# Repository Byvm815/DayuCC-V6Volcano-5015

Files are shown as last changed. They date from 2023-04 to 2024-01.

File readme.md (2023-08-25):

# 项目说明
## 托管
本项目使用Git做数据管理，托管在[Github](https://github.com/Byvm815/DayuCC-V6Volcano-5015)

如果你是在大鱼QQ群里下载的，建议你在下载后拉取更新

## 推荐的方案
我推荐你使用最新的V6方案B，也是我比较满意的方案。

需要说明的是，方案B的设计在大鱼TT公布前就已经想好了，没有抄袭TT的风道。

# 技术路线（摘抄自本人笔记）
## CR10路线
### 原版散热器，v6火山
优点：便宜、cc原版散热器，适配性最好、火山加热块可直接使用

缺点：喉管只有一个顶丝固定点，长时间的稳定性差、喉管接触方式导致接触面积小，喉管导热不佳（可通过硅脂解决）。稳定性差点，价格最便宜。

### 原版散热器，适配版火山加热块
优点：CC的理想热端、原版的双螺丝稳定、火山长度加热区

缺点：目前而言，没有硅胶套（但是我问客服，有非量产版的）、喉管的接触方式导致接触面积小，喉管导热不佳（可通过硅脂解决）。价格太贵，加上买喉管的钱，都够买cr10s（方块状）一套了。

### cr10（v6螺纹）散热器，v6火山加热块
优点：配件总价格最便宜、我想要的cr10散热器外形配v6喉管

缺点：散热片太少（暂时不确定是否有影响，因为螺纹有效地增大了喉管与散热器的接触面积）。就算散热够用，性价比也没有cr10s pro打印一个增高垫的方案高。

### cr10s散热器（方块状），v6火山
优点：直接使用m7的双金属喉管，CR10路线性价比最高的方案，到手可用。风道使用原版加长即可。

缺点：喉管中下段往上，喉管裸露，散热面积较小

### cr10s pro散热器，v6火山
优点：皆据上述的散热器优点：v6螺纹、多散热片、直接使用v6加热块、独有的双顶丝固定。

缺点：气动接头的位置过于靠上，在不安装气动接头的情况下，位置刚刚够用，无法直接安装气动接头（主要是空间大，挤出的耗材容易折弯）（我已经想到解决办法了。一，给电机底座加个垫片，再使用隐藏式的气动接头，通入特氟龙管。二，直接限制内部空间，具体设计有难度）（通过淘宝的散热器类型可知，这个就是参考cr6的散热器上端设计的，原版的cr6和cr10一样，气动接头安装的地方是平的，只是cr6要使用一个额外的延长座，结果cr10s pro直接把延长座和散热器合体了）

### cr10散热器外观的拓竹热端
优点：CC的理想热端

缺点：和cr10一样喉管导热差、很贵

## v6路线
之前一直想找螺纹长的铜柱，没有理想的。今天走狗屎运碰到了，m3*30+10，虽然螺纹长度差了一点，但拧入距离也有6mm了，完全够用。（其实可以通过两个铜柱连接的方式取代这个理想铜柱，我是傻瓜）

可以将固定''热端安装板''的螺丝替换成铜柱，就能在固定的同时，提供风扇固定孔了。这样，就可以使用cnc的金属v6固定座。风扇通过螺丝加紧固定，也比打印的孔位牢靠。

## 总结
CR10路线的散热器，便宜的没有一个是设计优秀的，设计优秀的又贵得要死（主要还是散热器无法单独购买）。

所以还得是V6，用网上的热门话语来说就是：V6 永远的神！

目前还没有理想的自动调平的方案（大鱼做的时候没考虑，硬件缺陷），代思路明确再设计验证。

# 开源许可证
本项目以AGPL协议开源。禁止商用，禁止售卖资料！

一切违背开源协议、侵犯原作者著作权、占有他人劳动成果用于盈利的行为，需自行承担法律风险！

# 捐赠
设计、测试、整理不易，可以捐赠1、2块。就当是研发费了。

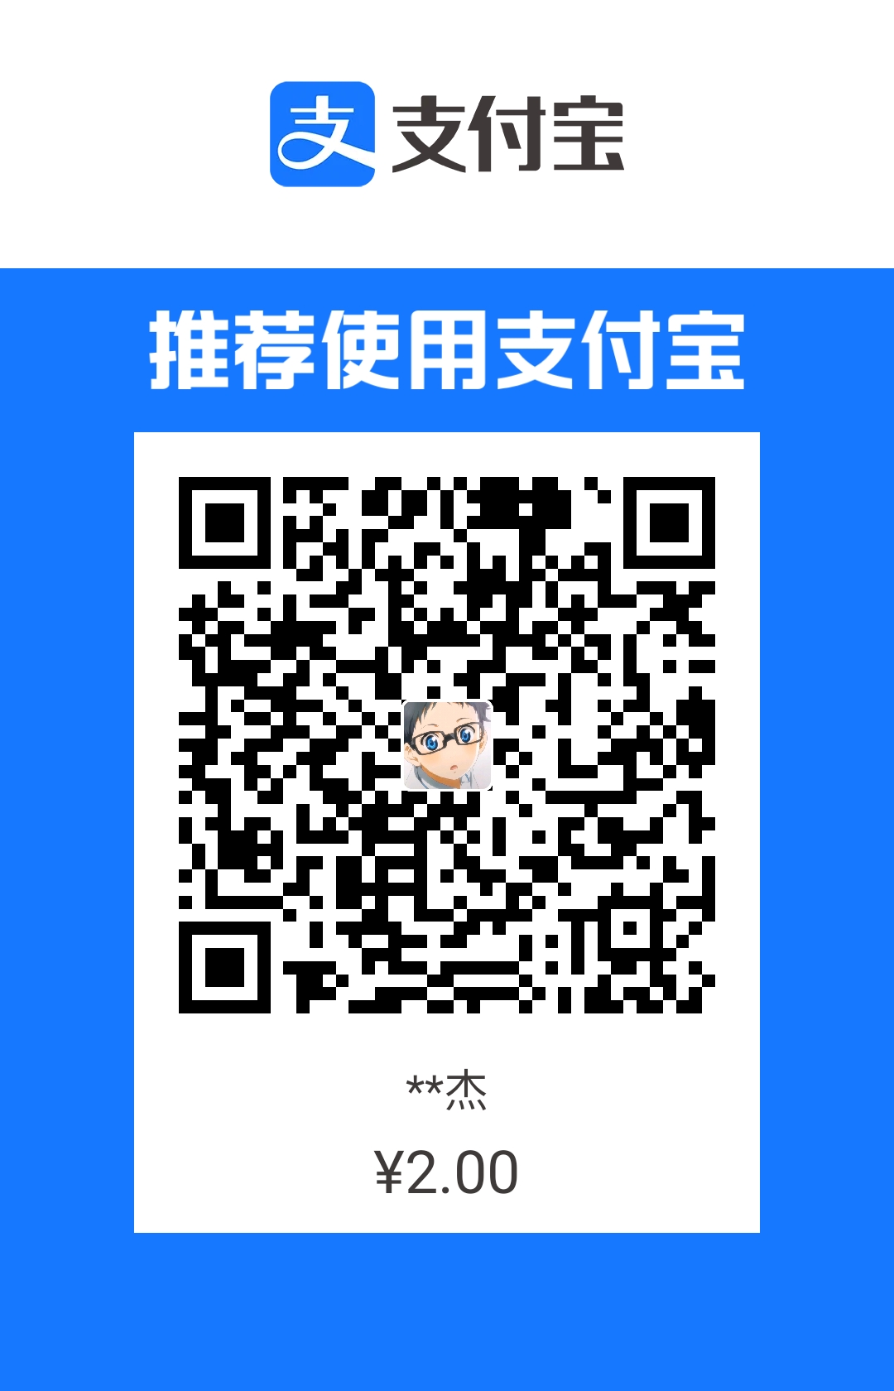
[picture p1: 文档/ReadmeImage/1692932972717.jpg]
收款码


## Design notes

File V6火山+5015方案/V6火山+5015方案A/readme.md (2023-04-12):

# 白雨木的说明

## 效果图（图片仅供参考）
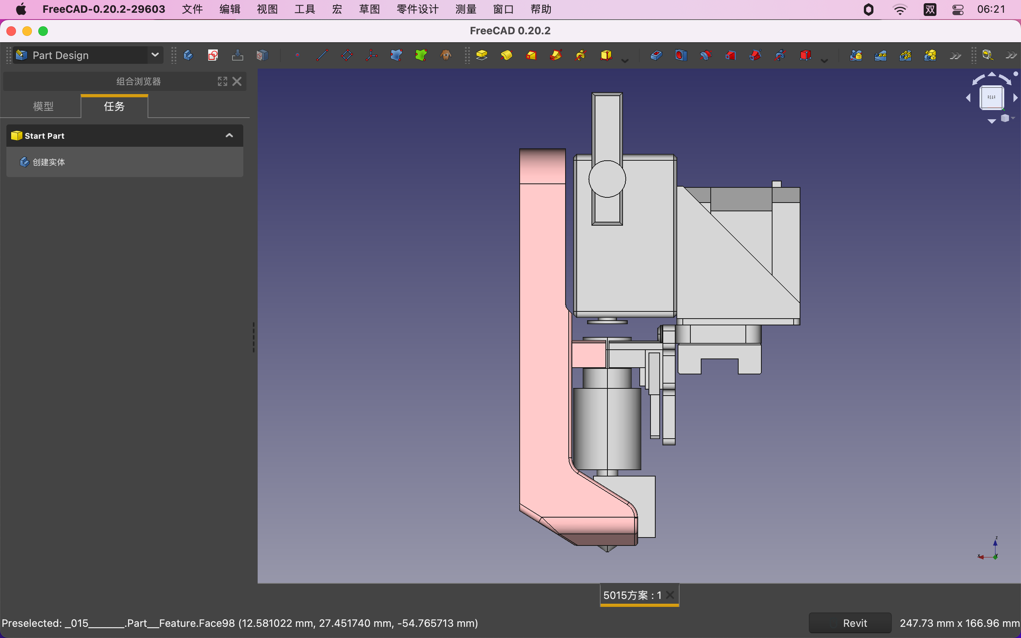
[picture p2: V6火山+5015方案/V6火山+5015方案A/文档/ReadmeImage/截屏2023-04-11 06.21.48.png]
截屏


## 物料清单：
1. [5015液压风扇](https://item.taobao.com/item.htm?spm=a1z09.2.0.0.4e562e8dwG9V3d&id=654878833029&_u=b3u8db4m4d76)
2. [M3*50螺丝](https://detail.tmall.com/item.htm?_u=b3u8db4mfd2b&id=636577427255&spm=a1z09.2.0.0.4e562e8dwG9V3d)
3. [M4*15对锁螺丝](https://detail.tmall.com/item.htm?id=542579355142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)
4. [E3DV6近程散热器](https://item.taobao.com/item.htm?spm=a1z10.3-c-s.w4002-17331600343.22.254e3e69IKgMQ4&id=559984859809)
5. [不锈钢喉管（不带铁氟龙）](https://item.taobao.com/item.htm?id=559690409325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)（双金属带外六角的喉管，比常规喉管长，我现在没有实物，故模型暂未适配）
6. [V6火山PT100铝加热块](https://item.taobao.com/item.htm?spm=a1z10.3-c-s.w4002-17331600343.29.c8e43e69NdG7as&id=680651648360)（推荐购买此加热块）
7. [热敏电阻](https://item.taobao.com/item.htm?spm=a1z10.3-c-s.w4002-17331600343.50.40003e6958S0JV&id=575202356478)（按加热块型号购买）
8. [硅胶套](https://item.taobao.com/item.htm?spm=a1z10.3-c-s.w4002-17331600343.19.c8e43e69uqzWFz&id=633630275262)（按加热块型号购买）
9. [火山喷嘴](https://item.taobao.com/item.htm?spm=a1z10.3-c-s.w4002-17331600343.38.436d3e69l3Q1HW&id=691269644652)

10. 3010风扇（CC清单已购）
11. M3*14螺丝（CC清单已购）
12. 加热棒（CC清单已购）
13. M3*10螺丝（CC清单已购）

不含已购物料和运费，共计38.91元。含运费，共计43.91元。

## 切片说明（以PrusaSlicer为例）
导风口需按以下条件进行特殊设置：
1. 0.4打印喷嘴，需要将“最小轮廓数”改为2，以便搭桥起点下方不悬空
2. （填充图案为星型时）“填充率”至少设为40%
3. 取消“自动生成支撑”，导风口可无支撑打印

贴墙端需按以下条件进行设置：
1. （填充图案为星型时）“填充率”至少设为40%

切片摆放方向：螺丝孔洞与Z轴平行。

## 改进空间
1. 取消3010风扇安装座，直接在开口平面上安装3015风扇，理论上与散热器之间有0.4mm距离
2. 贴墙端固定件可使用热熔滚花螺母

## Github
[项目地址](https://github.com/Byvm815/DayuCC-V6Volcano-5015)

## 开源许可证
本项目的导风口作者为【大鱼DIY】（以下简称“原作者”），原作者授权给白雨木进行二次更改并允许开源。原作者的开源条件是：开源后不可进行商用，故本项目以AGPL协议开源。禁止商用，禁止售卖资料！

一切违背开源协议、侵犯原作者著作权、占有他人劳动成果用于盈利的行为，需自行承担法律风险！

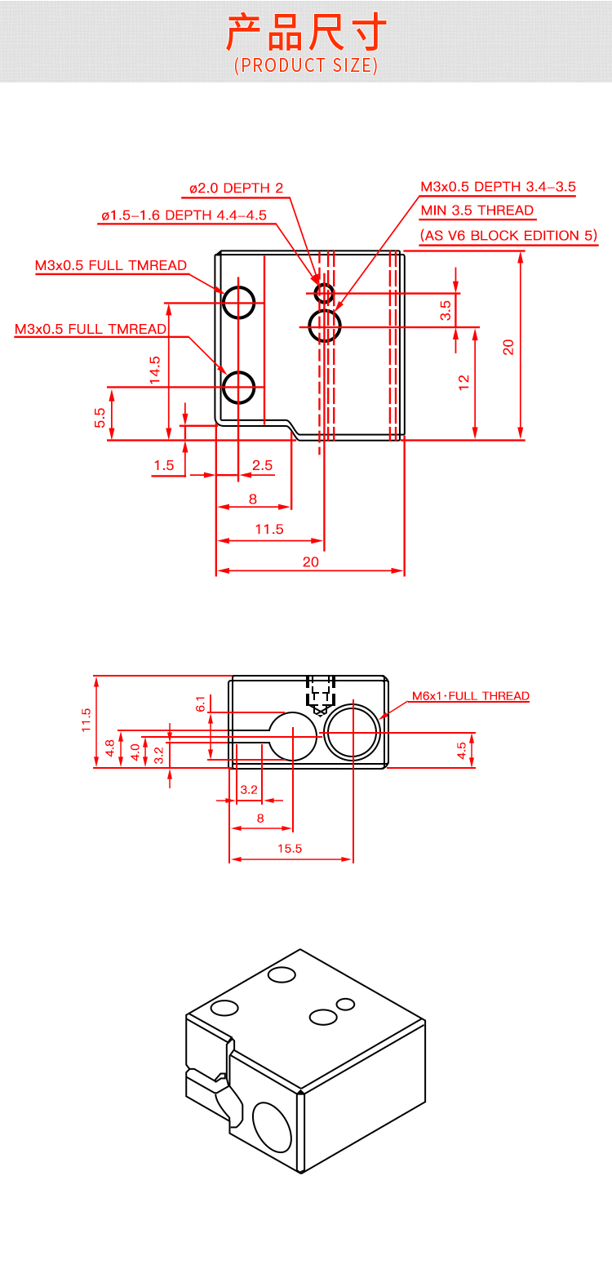
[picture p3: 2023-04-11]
V6火山+5015方案/参考资料/O1CN012gRX7m1FdcYz98SY7_!!3878490510.jpg

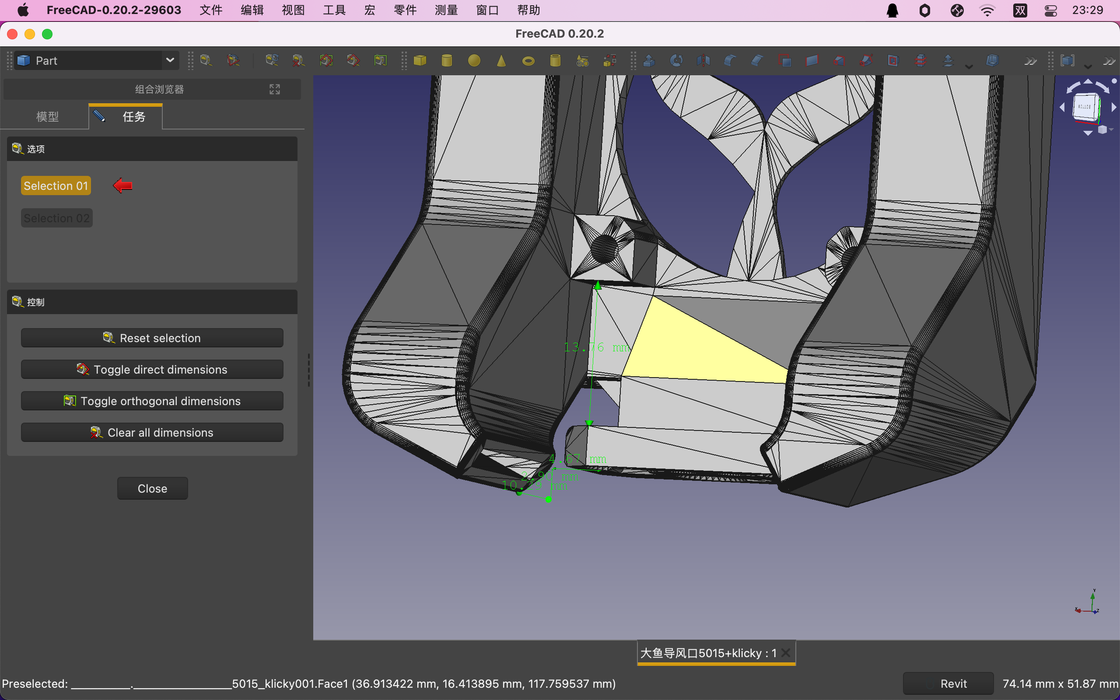
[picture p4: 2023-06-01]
V6火山+5015方案/参考资料/截屏2023-05-20 23.29.21.png

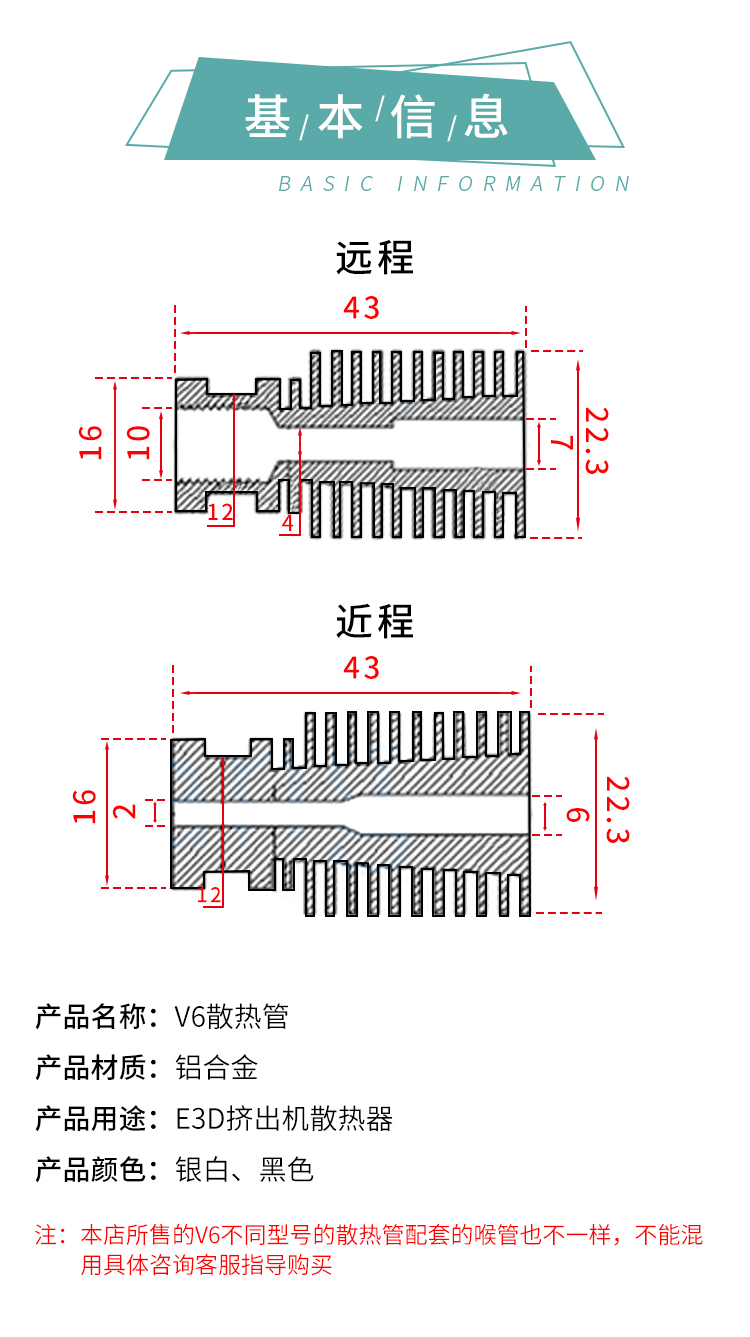
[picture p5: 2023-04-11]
V6火山+5015方案/参考资料/O1CN01hj3WWK1FdcZCZzyd2_!!3878490510.jpg

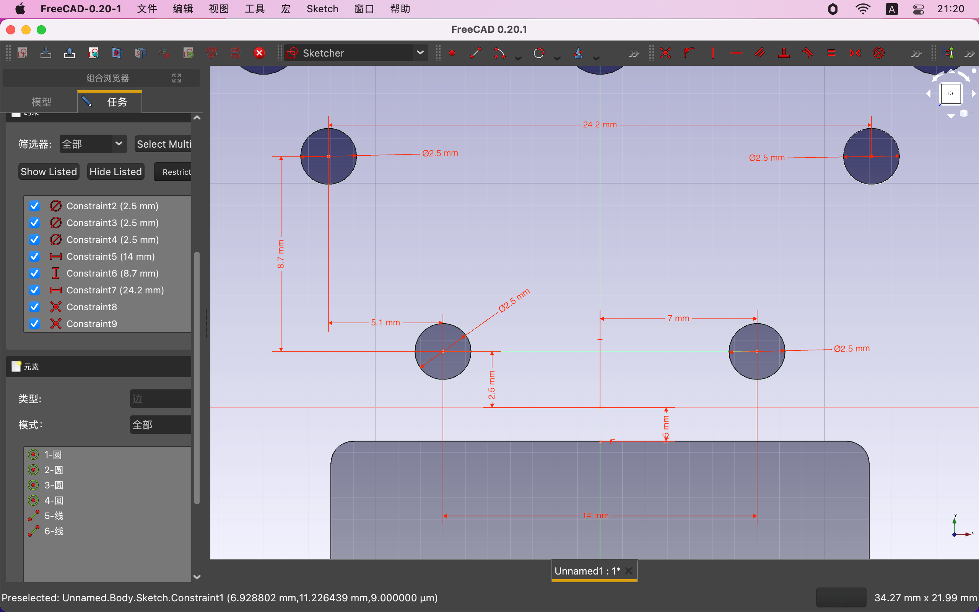
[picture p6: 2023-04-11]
V6火山+5015方案/参考资料/截屏2023-01-09 21.20.55.png

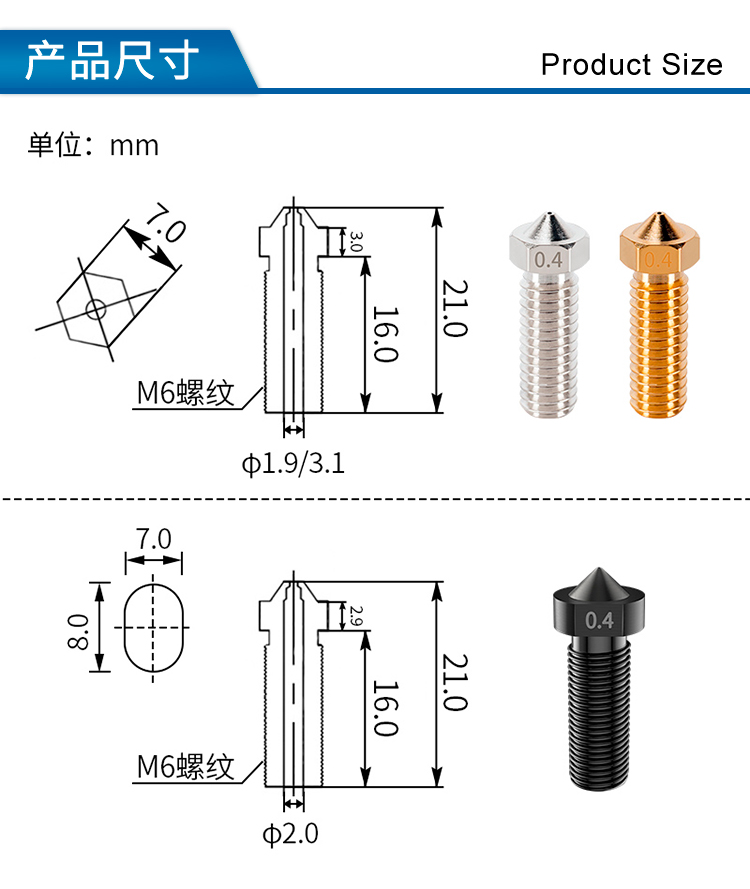
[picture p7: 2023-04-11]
V6火山+5015方案/参考资料/O1CN01lO3DwQ2JRxHx6H1lr_!!3319579419.jpg

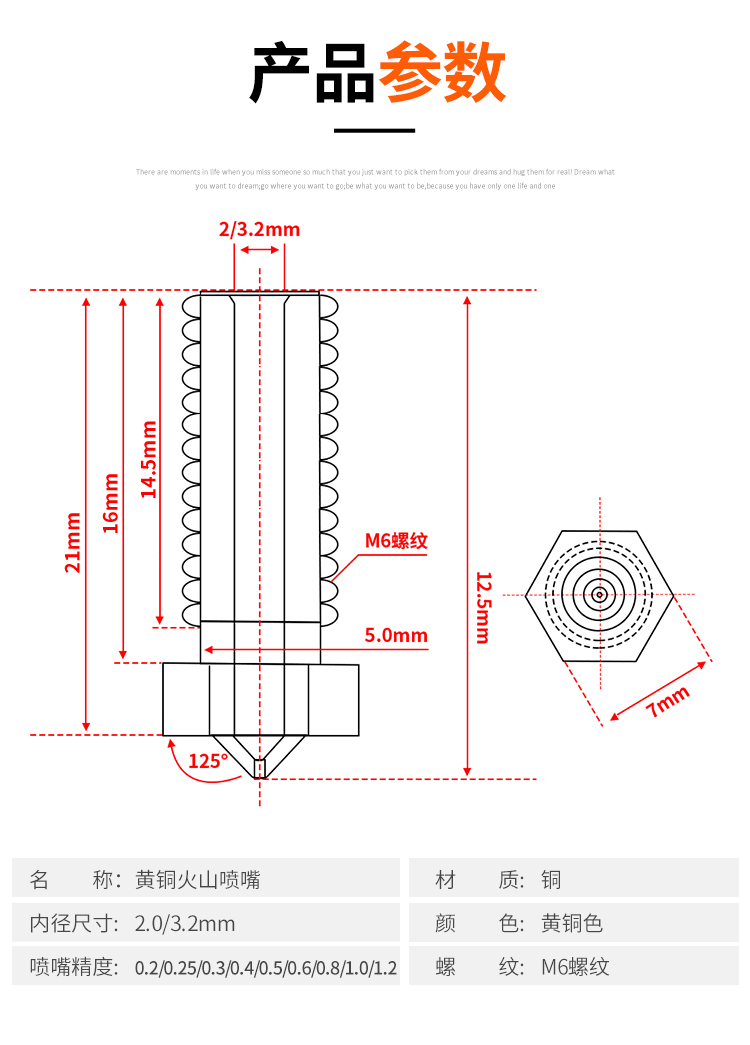
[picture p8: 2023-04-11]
V6火山+5015方案/参考资料/O1CN01tl6hNs1FdcdDW7SfI_!!3878490510.jpg

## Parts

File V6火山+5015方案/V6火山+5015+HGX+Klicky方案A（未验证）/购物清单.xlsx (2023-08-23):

 | 名称 | 价格 | 运费 | 总价 | 备注 | 链接
风道固定 | 5015风扇 | 6 |  | 6 |  | https://item.taobao.com/item.htm?spm=a1z09.2.0.0.7cdf2e8dv5TSCc&id=654878833029&_u=m3u8db4md1ac
 | M3*10+10 | 1.62 |  | 1.62 |  | https://detail.tmall.com/item.htm?_u=m3u8db4m3311&id=723347838083&skuId=5029218821605
 | M3*28+8 | 1.91 |  | 1.91 |  | https://detail.tmall.com/item.htm?_u=m3u8db4m671f&id=526408734762&skuId=4870769705726
 | M3*20 | 1.4 |  | 1.4
热端固定 | M3*3+3 | 0.92 |  | 0.92 | 可自行使用双通螺柱替换，或使用垫片 | https://detail.tmall.com/item.htm?id=723347838083&skuId=5029218821646
 | M3*16 |  |  | 0 | CNC夹紧件自带
 | M3*8 |  |  | 0 | CC清单已购
 | CNC夹紧件 | 9.6 |  | 9.6 |  | https://item.taobao.com/item.htm?spm=a1z09.2.0.0.7cdf2e8dv5TSCc&id=661998667872&_u=m3u8db4m8b0d
热端 | 3010风扇 |  |  | 0 | CC清单已购
 | V6风扇固定座 | 0.8 | 5 | 5.8 |  | https://item.taobao.com/item.htm?spm=a1z10.3-c-s.w4002-22464691177.19.6e8e52d6ffWhPJ&id=520650475697
 | V6内置接头版 | 3 |  | 3 | 注意螺纹尺寸即可，也可自行购买 V6近程散热器-M7螺纹 | https://item.taobao.com/item.htm?spm=a1z0d.6639537/tb.1997196601.12.37af7484v1LHsb&id=45264546491
 | 尾部M7螺纹外六角喉管 | 6.9 | 2.8 | 9.7 | 可自行购买 M7螺纹的不锈钢喉管，并更改模型 | https://item.taobao.com/item.htm?id=726282961254&ns=1&abbucket=12
 | PT-100加热块 | 4 |  | 4 |  | https://item.taobao.com/item.htm?spm=a1z10.3-c-s.w4002-22464691177.19.278152d6YCgUxj&id=703751758876
 | PT-100加热块硅胶套 | 1.2
 | 喷嘴 | 1.2 |  | 1.2 |  | https://item.taobao.com/item.htm?spm=a1z10.3-c-s.w4002-22464691177.9.278152d6YCgUxj&id=543290465385
 | PT-100热敏电阻-1M | 2.05 |  | 2.05 |  | https://item.taobao.com/item.htm?spm=a1z10.3-c-s.w4002-22464691177.9.6d3552d6S3S0Ja&id=40596831336
 | 加热棒 |  |  | 0 | CC清单已购
 |  |  |  | 47.2 | 需要说明的是，有的链接的商品只是和我用的型号相同 其次，商品可能会下架、替换、加价，造成的额外费用与本人无关，需自行按所给型号甄别

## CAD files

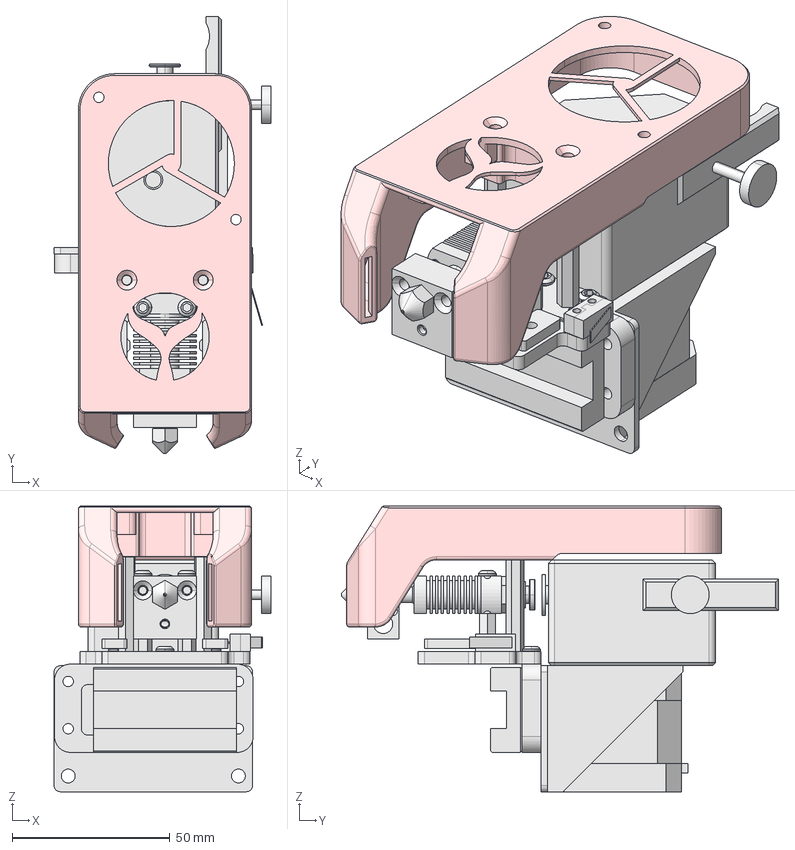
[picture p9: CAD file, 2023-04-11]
CR10+5015原始方案/CR10.FCStd
68.8 x 138.6 x 90.6 mm
CR10¼ÓÈÈ¿é20¡Á20¡Á10
CR10º_ֱͨ
MK8»ǍƧجM6
G1_8Ǹ¶¯½ԍ·PC4-01
эОλ¿ª¹ֱA125V003
MGN12H»¬¿002
CR10ɢɈ¹
ɢɈ¹ܰ²װ°
µ¥Í·ÂÝÖùM3¡Á12-4
µ¥Í·ÂÝÖùM3¡Á12-005
Í¬²½´øÑ¹Æ¬
Í¬²½´øÑ¹Æ¬001
42²½½øµç»ú004
42²½½øµç»úÖ§¼Ü
MGN12H»¬¿ꗪ½Ӱ䞘ס
BMG¼·³ö»ú
ÄÚÁù½ÇÆ½Ô²Í·ÂÝ¶¤M3¡Á028
ÄÚÁù½ÇÆ½Ô²Í·ÂÝ¶¤M3¡Á029
ÄÚÁù½ÇÆ½Ô²Í·ÂÝ¶¤M3¡Á030
µ¥Í·ÂÝÖùM3¡Á30-4
µ¥Í·ÂÝÖùM3¡Á30-005
ÄÚÁù½ÇÆ½Ô²Í·ÂÝ¶¤M3¡Á16
ÄÚÁù½ÇÆ½Ô²Í·ÂÝ¶¤M3¡Á031
5015µ¼·耚µĸ±±¾

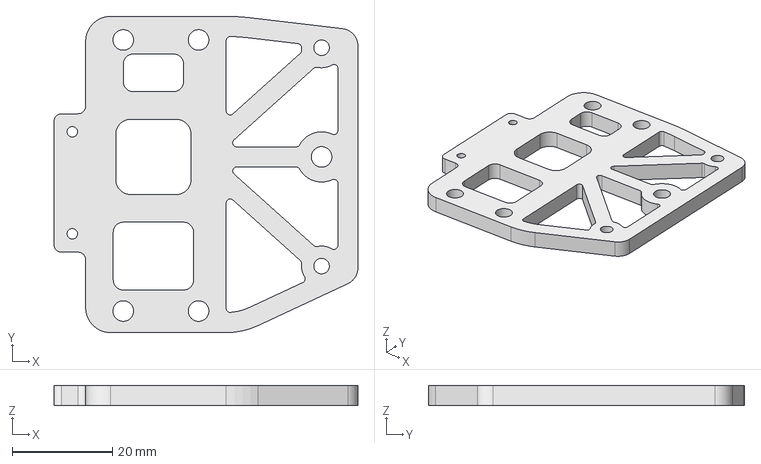
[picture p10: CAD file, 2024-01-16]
V6火山+5015方案/V6火山+5015+HGX+Klicky方案A（未验证）/HGX安装座-0mm.step
60.5 x 63.0 x 4.00 mm

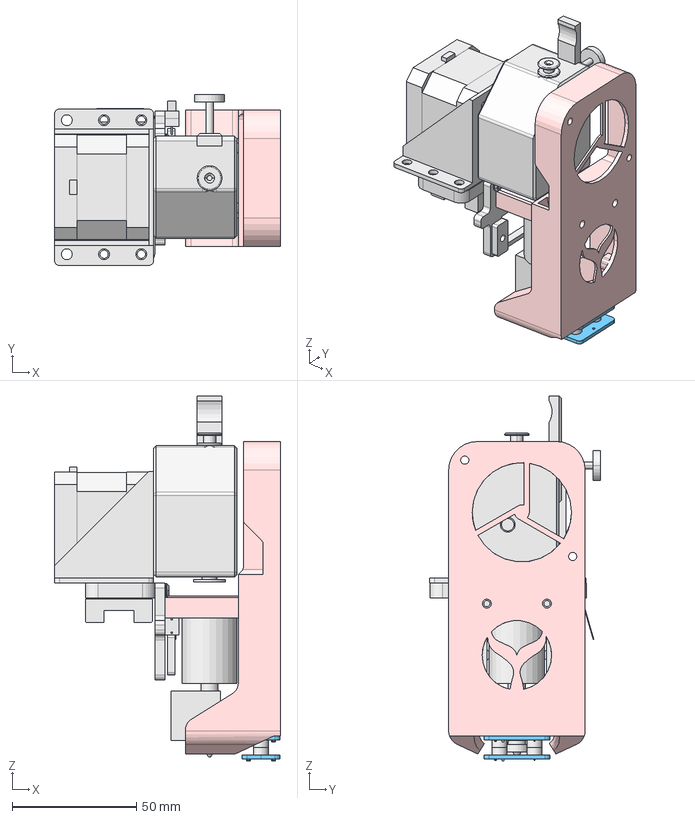
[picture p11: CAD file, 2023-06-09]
V6火山+5015方案/V6火山+5015+Klicky方案A（未完全验证）/V6火山+5015+Klicky方案A.FCStd
91.1 x 68.8 x 147.1 mm
E3DV6火山（玻璃热敏）
эОλ¿ª¹ֱA125V003
MGN12H»¬¿002
ɢɈ¹ܰ²װ°
Í¬²½´øÑ¹Æ¬
Í¬²½´øÑ¹Æ¬001
42²½½øµç»ú004
42²½½øµç»úÖ§¼Ü
MGN12H»¬¿ꗪ½Ӱ䞘ס
BMG¼·³ö»ú
ÄÚÁù½ÇÆ½Ô²Í·ÂÝ¶¤M3¡Á028
ÄÚÁù½ÇÆ½Ô²Í·ÂÝ¶¤M3¡Á029
ÄÚÁù½ÇÆ½Ô²Í·ÂÝ¶¤M3¡Á030
5015µ¼·耚-¿³ͷ

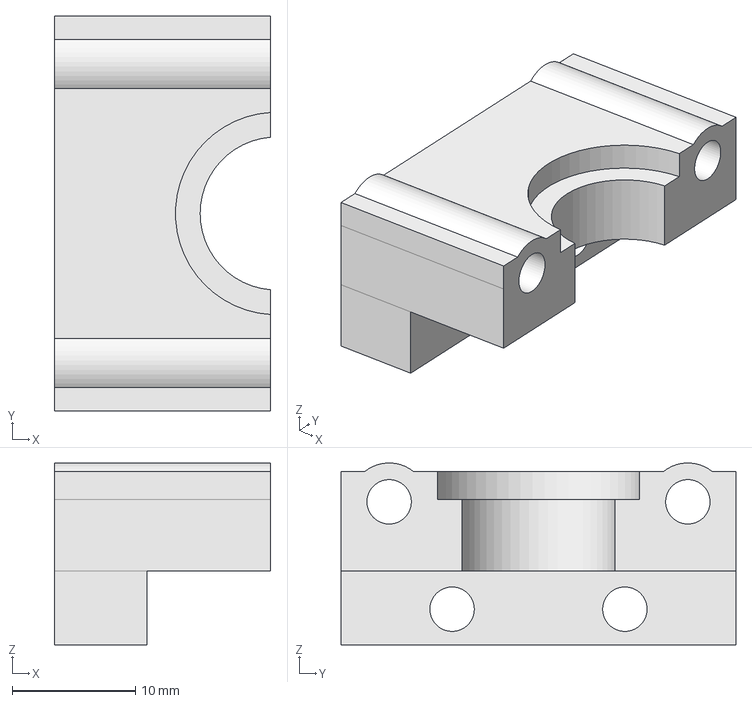
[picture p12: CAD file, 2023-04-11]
V6火山+5015方案/V6火山+5015方案A/STEP/V6火山+5015方案-贴墙端.step
17.5 x 32.0 x 14.7 mm

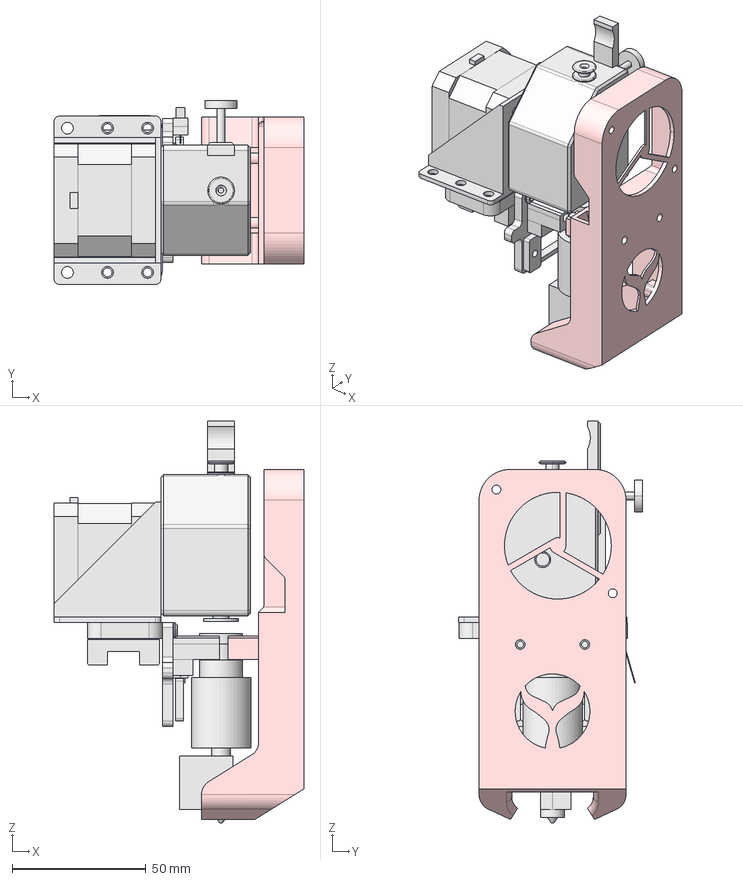
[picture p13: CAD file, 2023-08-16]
V6火山+5015方案/V6火山+5015方案A/工程文件/V6火山+5015方案.FCStd
93.5 x 68.8 x 150.5 mm
E3DV6火山（玻璃热敏）
эОλ¿ª¹ֱA125V003
MGN12H»¬¿002
ɢɈ¹ܰ²װ°
Í¬²½´øÑ¹Æ¬
Í¬²½´øÑ¹Æ¬001
42²½½øµç»ú004
42²½½øµç»úÖ§¼Ü
MGN12H»¬¿ꗪ½Ӱ䞘ס
BMG¼·³ö»ú
ÄÚÁù½ÇÆ½Ô²Í·ÂÝ¶¤M3¡Á028
ÄÚÁù½ÇÆ½Ô²Í·ÂÝ¶¤M3¡Á029
ÄÚÁù½ÇÆ½Ô²Í·ÂÝ¶¤M3¡Á030
贴墙端
5015µ¼·耚

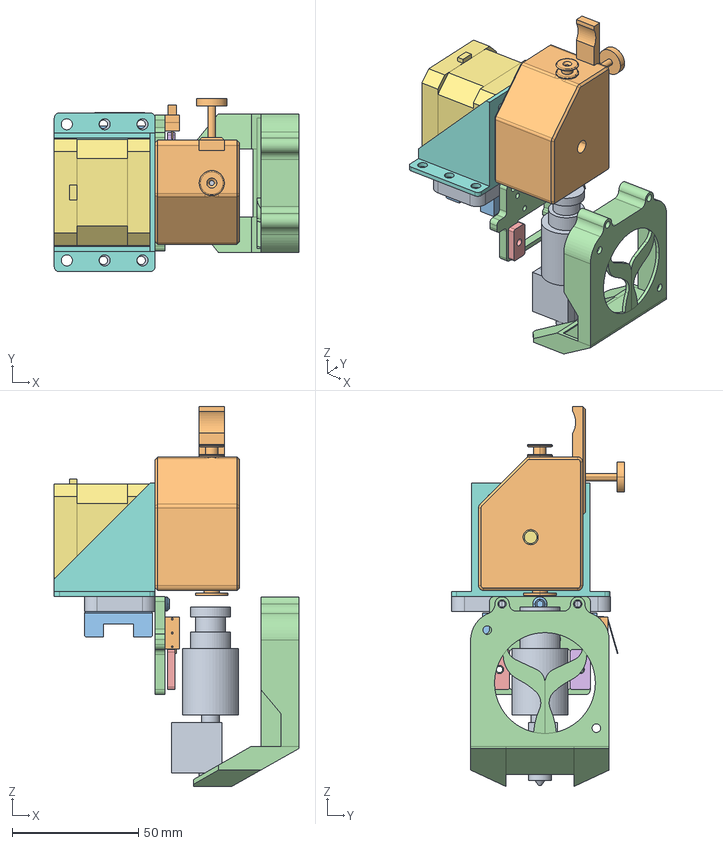
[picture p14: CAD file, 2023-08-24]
V6火山+5015方案/V6火山+5015方案B/V6火山+5015方案B.FCStd
97.0 x 68.8 x 150.8 mm
E3DV6火山（玻璃热敏）
эОλ¿ª¹ֱA125V003
MGN12H»¬¿002
ɢɈ¹ܰ²װ°
Í¬²½´øÑ¹Æ¬
Í¬²½´øÑ¹Æ¬001
42²½½øµç»ú004
42²½½øµç»úÖ§¼Ü
MGN12H»¬¿ꗪ½Ӱ䞘ס
BMG¼·³ö»ú
ÄÚÁù½ÇÆ½Ô²Í·ÂÝ¶¤M3¡Á029
合并上下

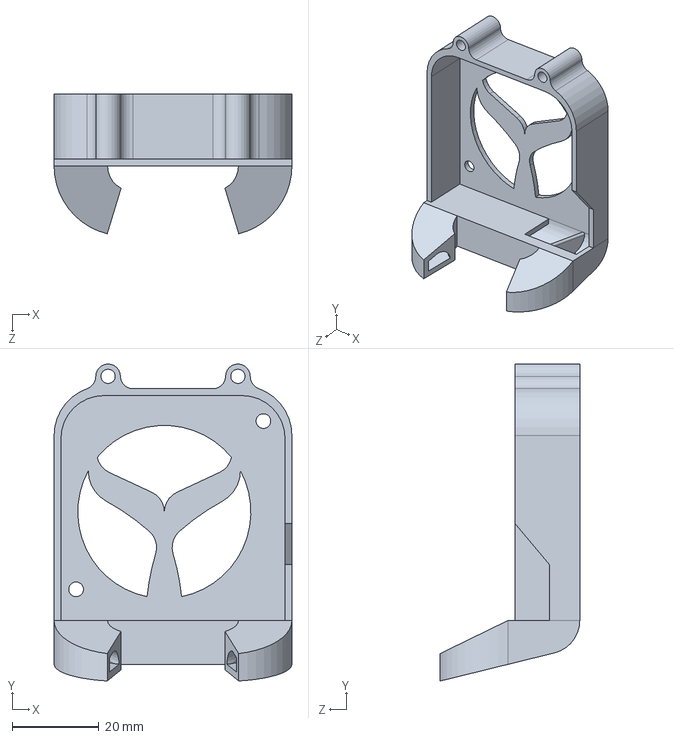
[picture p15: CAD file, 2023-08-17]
V6火山+5015方案/V6火山+5015方案B/不理想设计/V6火山+5015方案B.SLDPRT
55.0 x 73.3 x 32.3 mm

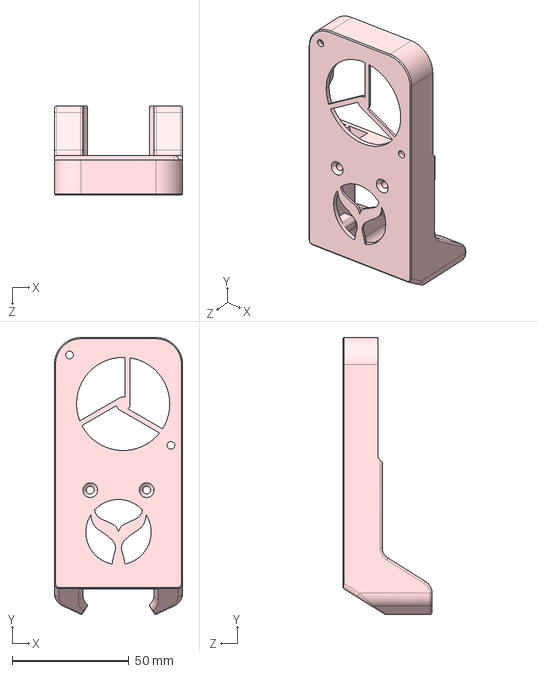
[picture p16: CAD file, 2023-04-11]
V6火山+5015方案/参考资料/【大鱼DIY】导风口/5015导风口的副本.STEP
55.0 x 118.9 x 38.4 mm

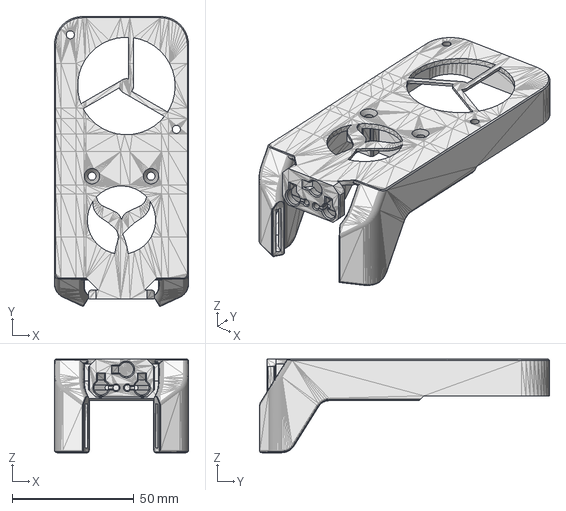
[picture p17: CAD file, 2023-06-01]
V6火山+5015方案/参考资料/大鱼导风口5015+原版klicky.FCStd
55.0 x 118.9 x 38.4 mm

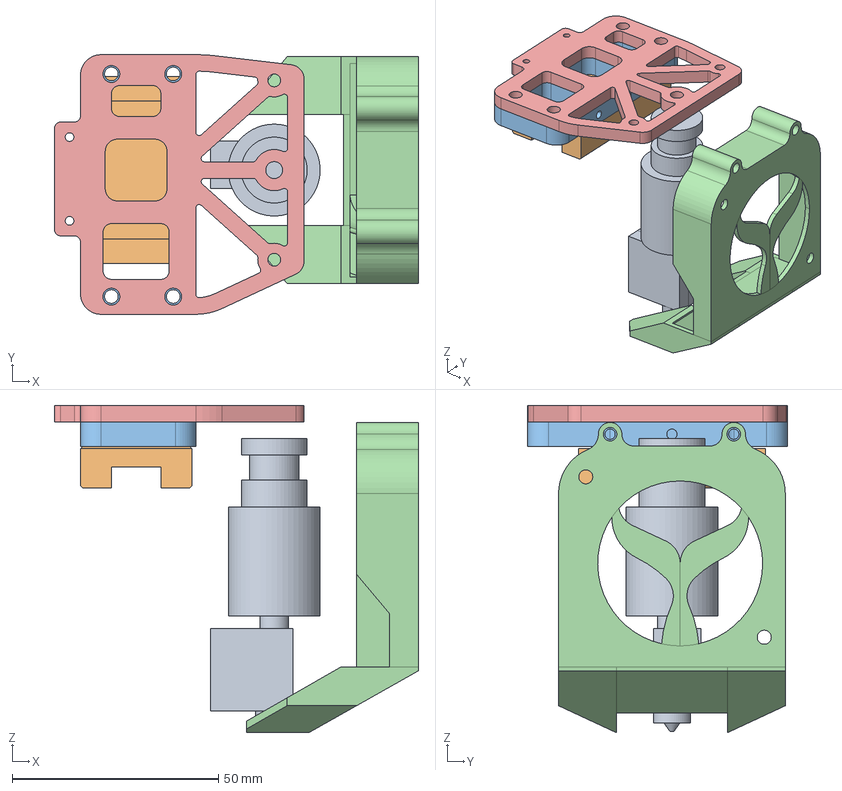
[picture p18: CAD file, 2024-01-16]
V6火山+5015方案/V6火山+5015+HGX+Klicky方案A（未验证）/V6火山+5015+HGX+Klicky方案A.FCStd
88.3 x 63.0 x 79.4 mm
E3DV6火山（玻璃热敏）
MGN12H»¬¿002
MGN12H»¬¿ꗪ½Ӱ䞘ס
导风道
HGX安装座+0mm

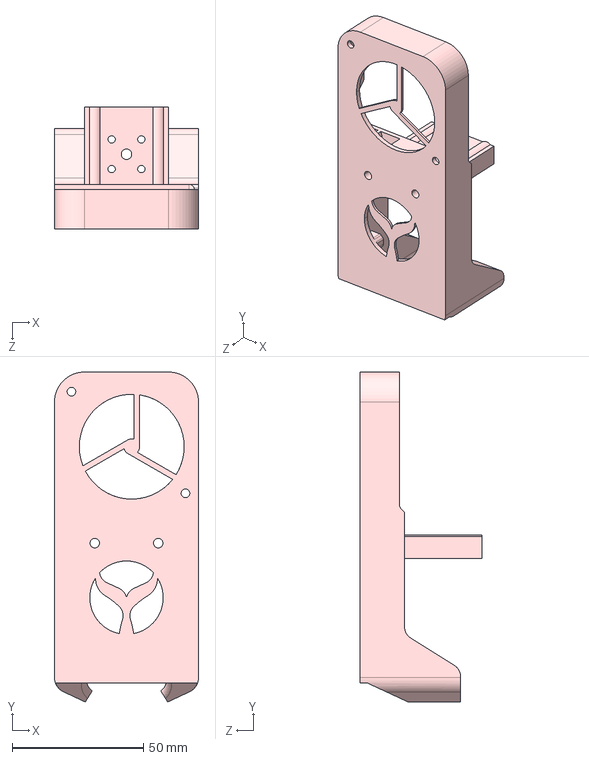
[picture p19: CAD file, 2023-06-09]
V6火山+5015方案/V6火山+5015+Klicky方案A（未完全验证）/5015导风口-砍头.STEP
55.0 x 125.9 x 46.5 mm

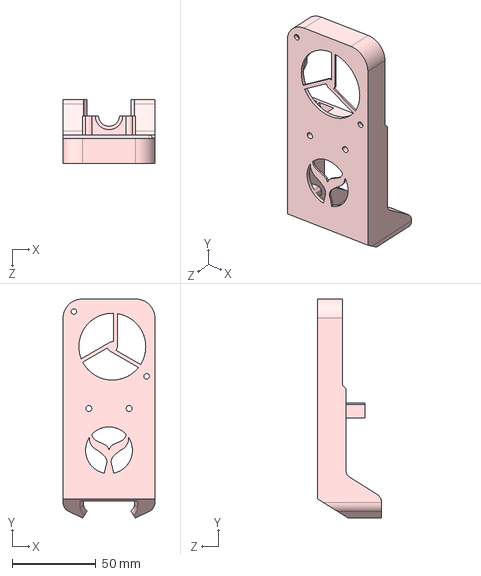
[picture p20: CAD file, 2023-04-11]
V6火山+5015方案/V6火山+5015方案A/STEP/5015导风口.STEP
55.0 x 131.0 x 38.4 mm

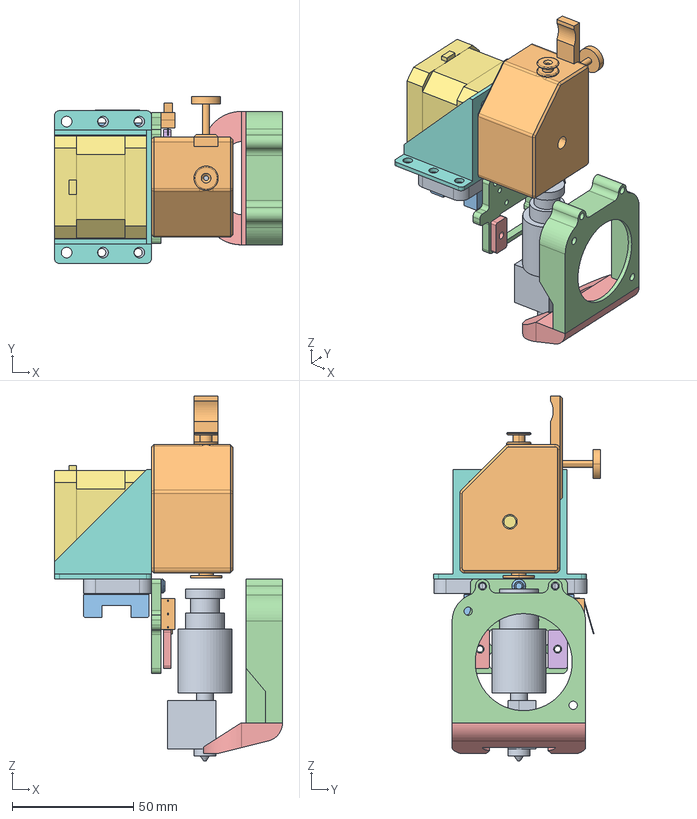
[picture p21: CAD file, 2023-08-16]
V6火山+5015方案/V6火山+5015方案B/不理想设计/V6火山+5015方案B-无法抽壳.FCStd
94.0 x 68.8 x 150.5 mm
E3DV6火山（玻璃热敏）
эОλ¿ª¹ֱA125V003
MGN12H»¬¿002
ɢɈ¹ܰ²װ°
Í¬²½´øÑ¹Æ¬
Í¬²½´øÑ¹Æ¬001
42²½½øµç»ú004
42²½½øµç»úÖ§¼Ü
MGN12H»¬¿ꗪ½Ӱ䞘ס
BMG¼·³ö»ú
ÄÚÁù½ÇÆ½Ô²Í·ÂÝ¶¤M3¡Á029
风扇安装座-风扇安装座
风扇安装座-导风道

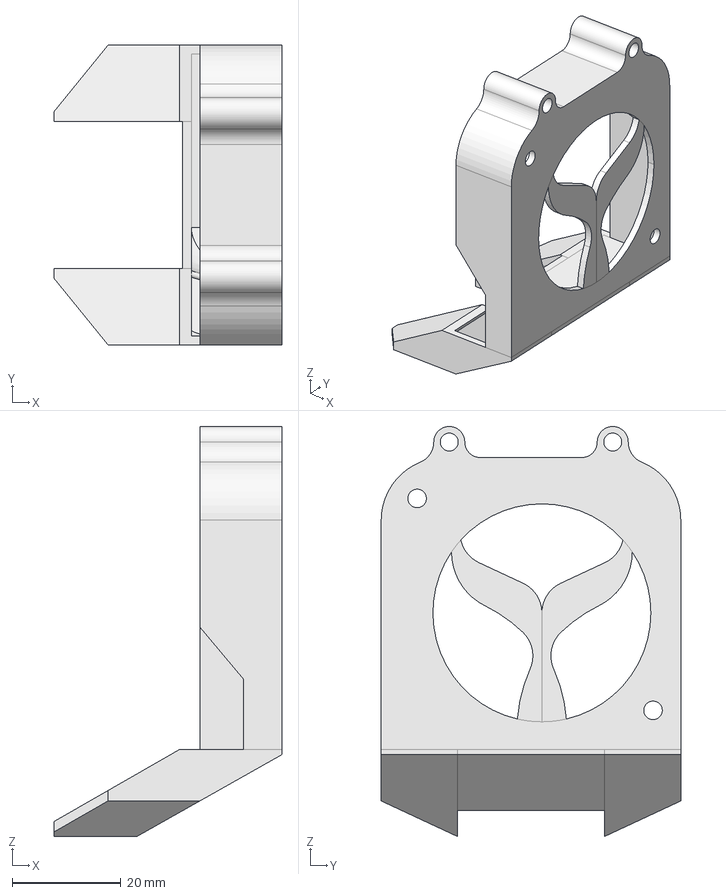
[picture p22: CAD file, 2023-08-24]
V6火山+5015方案/V6火山+5015+HGX+Klicky方案A（未验证）/导风道.step
41.8 x 55.0 x 75.3 mm

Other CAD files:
V6火山+5015方案/V6火山+5015方案A/工程文件/5015导风口.SLDPRT
V6火山+5015方案/V6火山+5015+Klicky方案A（未完全验证）/5015导风口-砍头.SLDPRT
V6火山+5015方案/参考资料/【大鱼DIY】导风口/5015导风口的副本.SLDPRT

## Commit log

2023-04-11 初始化仓库
    [5015导风口.SLDPRT, 5015导风口.STEP, 5015导风口的副本.SLDPRT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]
2023-04-11 添加开源许可证
2023-04-11 添加Github地址
2023-04-12 将双金属喉管替换为不锈钢喉管，因为双金属喉管长一点，模型不适配
2023-04-12 更改物料价格
2023-04-12 添加未加入的M3*10螺丝
2023-06-01 初步完成，待验证
    [5015导风口-砍头.SLDPRT, 5015导风口-砍头.STEP, V6火山+5015+Klicky方案.FCStd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]
2023-06-09 风道延长1.5mm，适配双金属喉管
    [5015导风口-砍头.SLDPRT, 5015导风口-砍头.STEP, V6火山+5015+Klicky方案.FCStd]
2023-08-16 重命名并移动
    [5015导风口.SLDPRT, 5015导风口.STEP, V6火山+5015方案-贴墙端.step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]
2023-08-16 初步完成
    [V6火山+5015方案B.FCStd, V6火山+5015方案B.SLDPRT, V6火山+5015方案B.STEP]
2023-08-17 优化高度、为添加长风道拐角处添加圆角
    [V6火山+5015方案B.SLDPRT, V6火山+5015方案B.STEP]
2023-08-22 添加。已完成第一次测试，本模型已经过改进：风道水平距离增长3mm、出风口倾角改为25度
    [V6火山+5015方案B.FCStd]
2023-08-22 添加。已初步完善
    [购物清单.xlsx]
2023-08-22 添加图案
    [V6火山+5015方案B.FCStd]
2023-08-23 优化风道安装座壁厚、优化风道结构、优化模型草图及其位置、风道加高1.5mm、添加注释
    [V6火山+5015方案B.FCStd]
2023-08-23 修改为V6内置接头的的散热器、修改为双金属喉管、添加示例图片
    [购物清单.xlsx]
2023-08-23 优化备注
    [购物清单.xlsx]
2023-08-23 修复风道布尔合并后，模型混乱破碎的问题
    [V6火山+5015方案B-合并上下.step, V6火山+5015方案B.FCStd]
2023-08-24 优化图案
    [V6火山+5015方案B-合并上下.step, V6火山+5015方案B.FCStd]
2023-08-24 修复搭桥草图依附错误
    [V6火山+5015方案B-合并上下.step, V6火山+5015方案B.FCStd]
2023-08-25 添加实物图
2023-08-25 添加readme
2024-01-14 添加*.FCBak
2024-01-14 HGX安装座初步完成
    [V6火山+5015+HGX+Klicky方案A-导风道.step, V6火山+5015+HGX+Klicky方案A.FCStd]
2024-01-15 完全约束
    [V6火山+5015+HGX+Klicky方案A.FCStd]
2024-01-16 优化，不记得干了什么
    [V6火山+5015+HGX+Klicky方案A.FCStd]
2024-01-16 复制V6火山+5015方案B的清单
    [购物清单.xlsx]
